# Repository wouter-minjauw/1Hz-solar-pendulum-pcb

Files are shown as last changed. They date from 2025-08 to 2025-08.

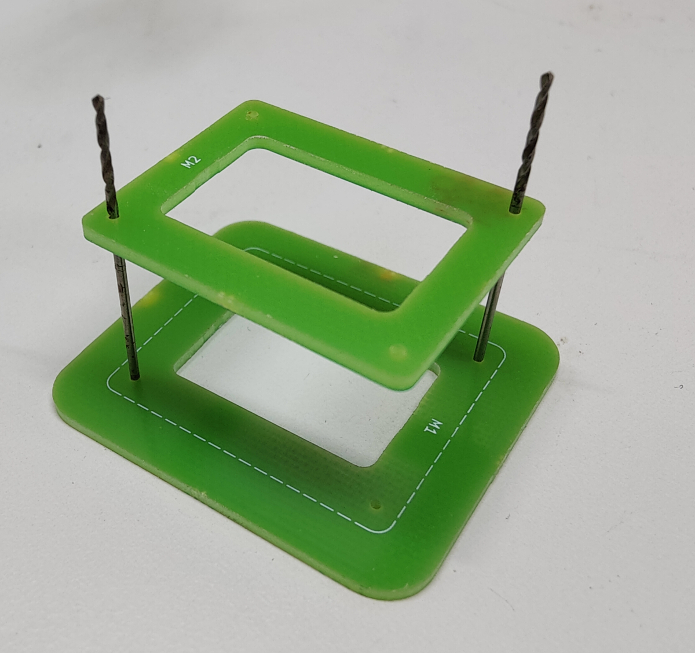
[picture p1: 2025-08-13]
pictures/coils/coil_former_assembly.jpg

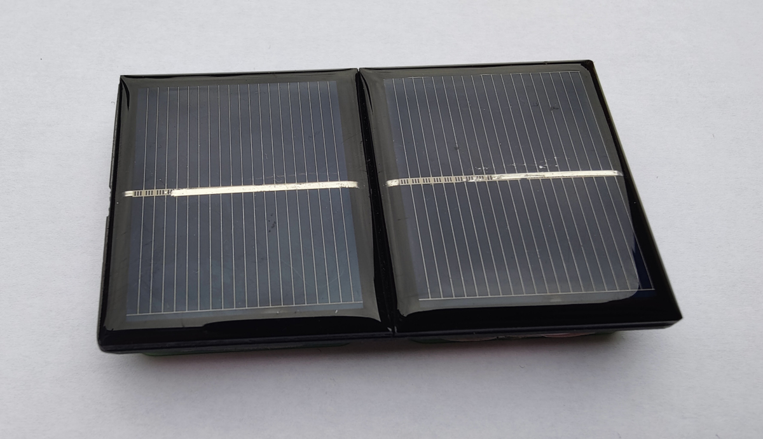
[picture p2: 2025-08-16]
pictures/coils/final_assembly_front.jpg

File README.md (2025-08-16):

# A 1Hz solar powered pendulum without transistors
## The pendulum
Nothing shows more what this is all about than a simple video of the pendulum in operation.

https://github.com/user-attachments/assets/9172c2cc-38bf-4e86-9793-8a3549da9c43

## The idea behind it
The idea behind this project was to create a solar powered pendulum in the simplest way possible, without any transistors. This is easier said than done, as most of us know how to design with transistors, but we have lost the knowledge to design something without them.

## The problem that needs to be solved
The problem is that in order to make the pendulum oscillate, some sort of AC force must be applied to the pendulum, but a solar cell provides DC output. So the main problem boils down to **can you generate an AC force on a mechanical system by using DC solar cells.**

The answer is yes, but it requires some out of the box thinking, and some may consider the solution as 'cheating'. However, the goal was not to use transistors, so anything is allowed as long as no transistors are used.

## Generating force
To generate force on the pendulum, a magnet is put on the pendulum, and coils are used below the magnet to push the magnet. The picture below shows a cross section of the two coils that are used in the device, and how current should be passed through them in order to generate a magnetic force to the right or to the left, depending on the direction of the current through the coils.
magnet_and_coils

## Creating an AC source with DC solar cells
If no transistors can be used to create an 'inverter' which turns DC into AC, a different solution is needed. A lot of experiments were performed with the pendulum partially shading it's own solar cell in order to get some AC voltage superimposed on the DC output of the solar cell, but the results were disappointing. Although you can get some AC voltage on top of the DC voltage, the power you can get out of it is very limited.

A much better solution turned out to be using two solar cells, and wiring them in anti-parallel, as can be seen in the following schematic of the device.

schematic

Each solar cell can be modeled as a light-dependent current source, with an intrinsic diode in parallel. If the pendulum is in the center, then both cells will be 50% shaded. The left solar cell pushes 200mA from GND to V_SOLAR, and the right solar cell pulls 200mA from V_SOLAR to GND. Both currents balance each other out, and no current flows through the intrinsic diodes of the cells, V_SOLAR is thereby 0V.

If the pendulum swings to the left, then the left solar cell will be (for instance) 75% shaded and the right solar cell 25% shaded. The left solar cell will now push 100mA from GND to V_SOLAR, the right solar cell will pull 300mA from V_SOLAR to GND. As Kirchoff's laws must be obeyed, 200mA will flow through the intrinsic diode of the right solar cell, resulting in V_SOLAR become a few hunderd millivolts negative. Similarly, if the pendulum swings to the right, V_SOLAR becomes a few hundred millivolts positive.

A sinusoidal movement of the pendulum results in a sinusoidal current of the solar cells, but due to the nonlinear I-V characteristic of the intrinsic diodes, the waveform of V_SOLAR starts to look more like a quare wave than a sine, which will turn out to be beneficial later on.

The pictures below show a simulation of the solar generator and the resulting V_SOLAR voltage. (The exact model of the diodes doesn't really matter, we just want to show the general behavior here.)

simulation_schematic
simulation_waveform

The dv/dt slope of the voltage is the highest at the zero crossings of the V_SOLAR, and this occurs when the pendulum passes through the mechanical center, shading both solar cells equally. Looking back at the magnetics picture earlier, this exactly when force should be generated on the magnet. In order to provide the right force at the right time, some capacitors in parallel are connected between V_SOLAR and the coils. Due to the I=C*dv/dt behavior of the capacitor, it will pass the most current through the coils at the zero crossings of the waveform, and that's exactly when we need it.

## The panelized PCB
A panelized PCB was made for this project, which contains a base PCB on which the solar cells are directly mounted, and some smaller PCBs which can be used to create coil formers. As I don't have a 3D printer yet, and needed a PCB anyway, it was the most economical solution to make the coil former out of PCB material.

All PCB's have 1mm alignment holes. The coil formers are built by using 1mm HSS drills as alignment guides, and stacking the different PCB's on top of each other with some superglue between them.

coil_former_assembly
assembled_coil_former

The coils are wound with 1000 turns of very fine wire. At the ends of the fine wire, a thicker wire was attached for mechanical rubustness, and the windings were covered with some paint masking tape for protection.

The final assembly looks like this:

final_assembly_front
final_assembly_back

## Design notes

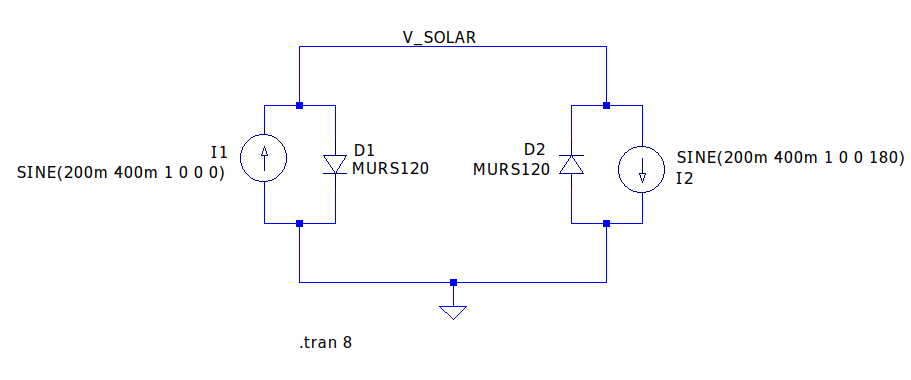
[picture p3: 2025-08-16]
pictures/theory_of_operation/simulation_schematic.png

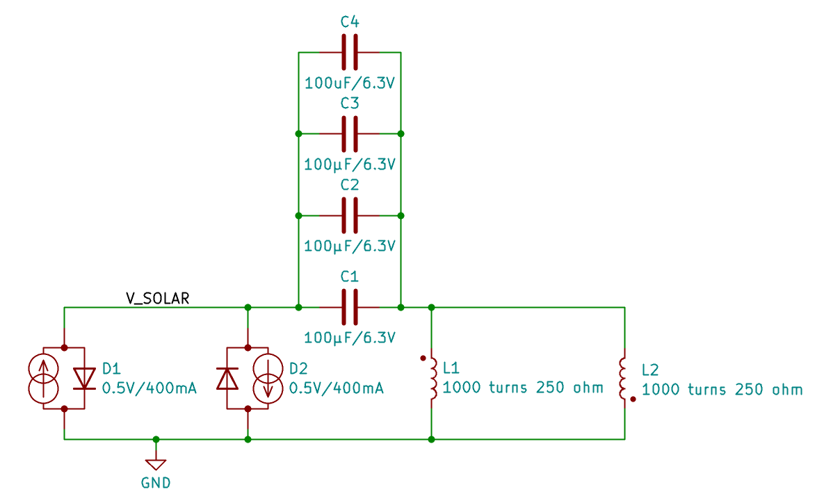
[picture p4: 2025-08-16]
pictures/theory_of_operation/schematic.png

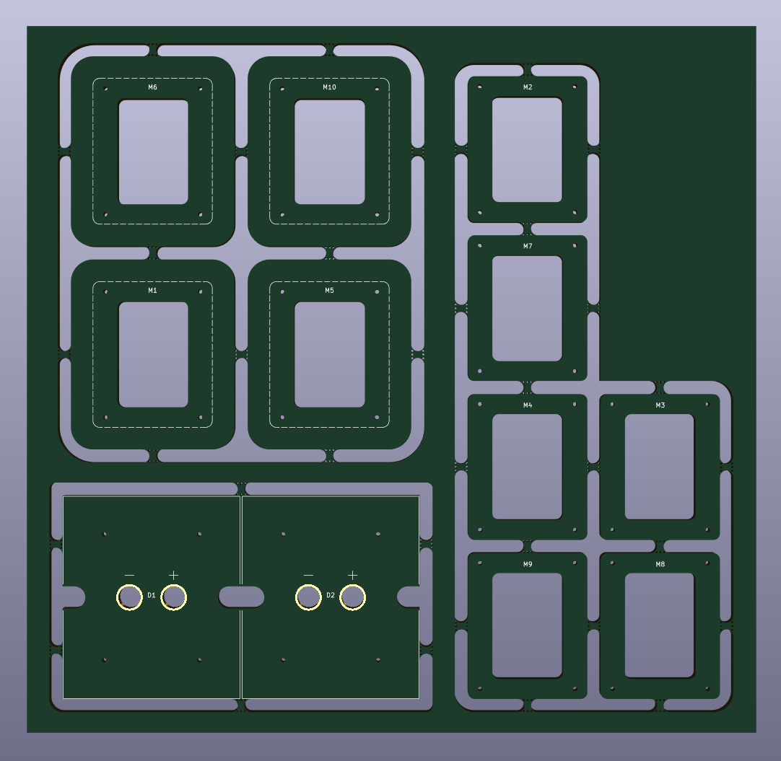
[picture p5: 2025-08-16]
pictures/panelized_pcb/panelized_pcb.png

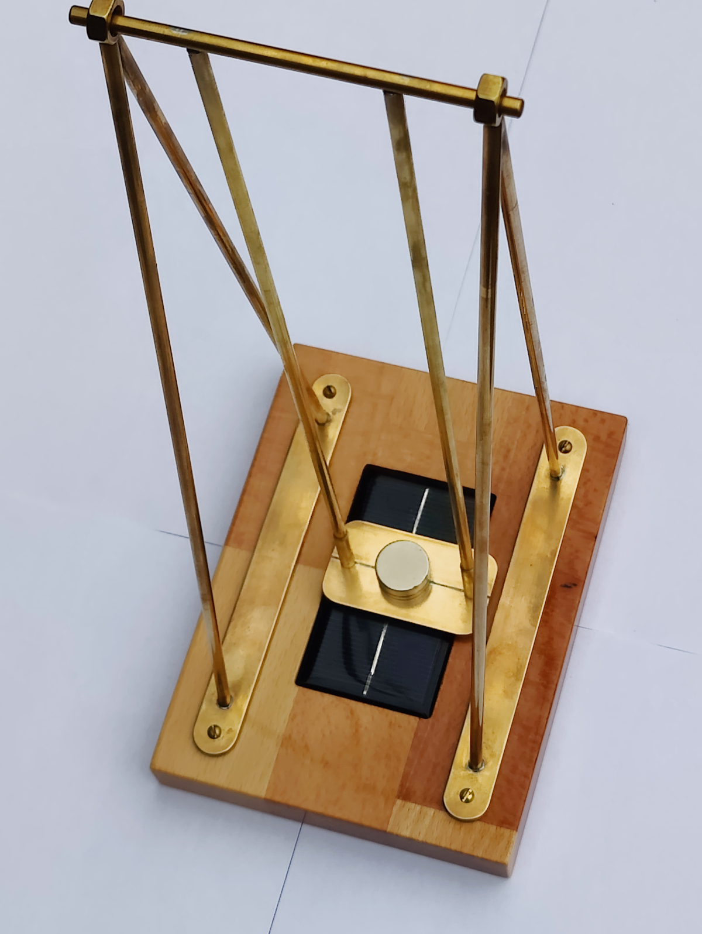
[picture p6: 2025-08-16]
pictures/pendulum/finished_pendulum.jpg

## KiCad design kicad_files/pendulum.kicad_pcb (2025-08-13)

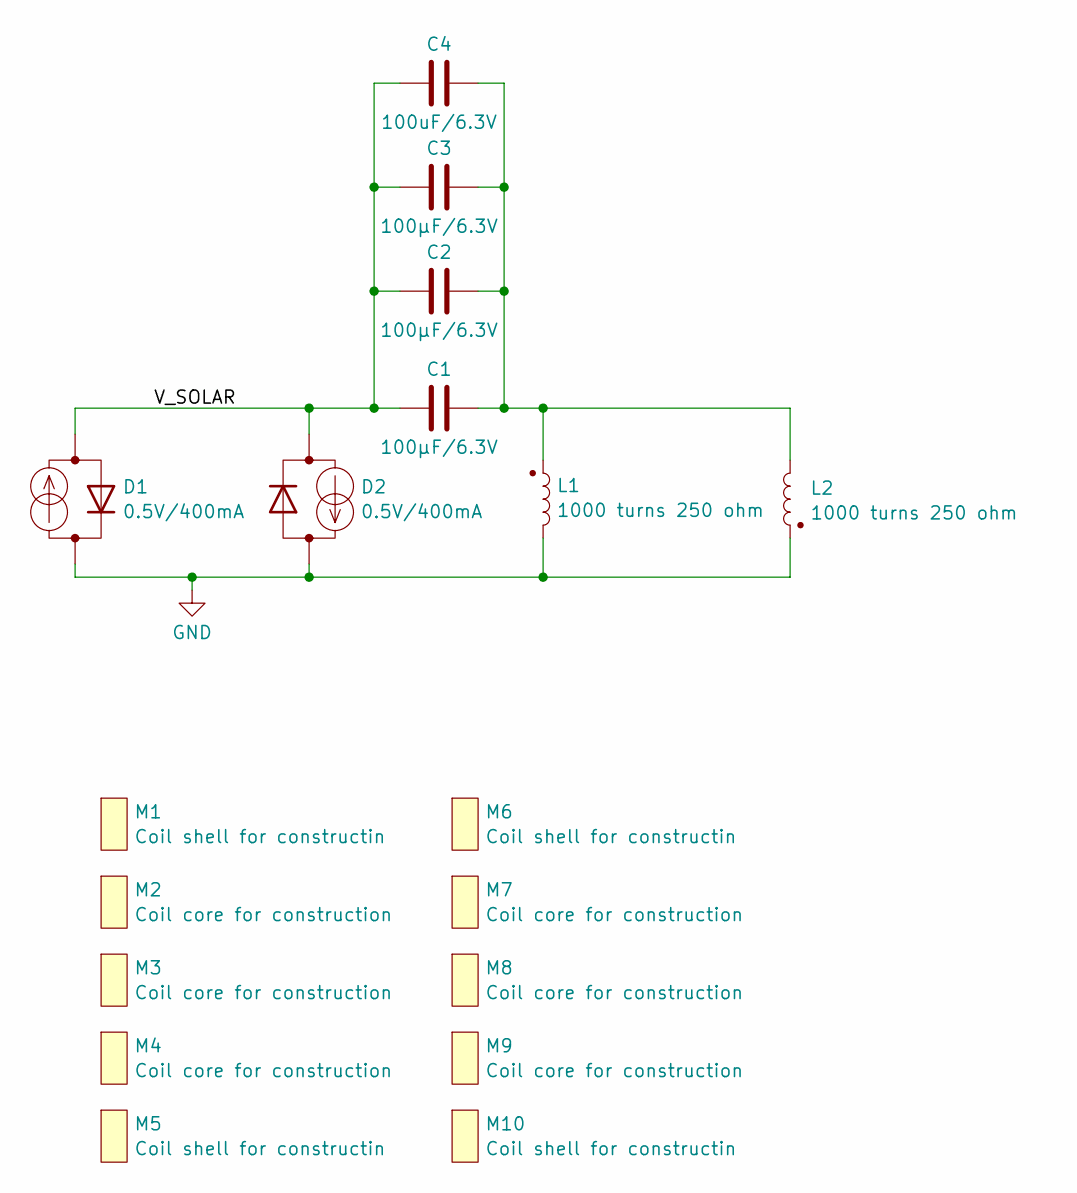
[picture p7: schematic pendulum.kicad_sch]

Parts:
C1, C2, C3: 100µF/6.3V; C_1206_3216Metric_Pad1.33x1.80mm_HandSolder
C4: 100uF/6.3V; C_1206_3216Metric_Pad1.33x1.80mm_HandSolder
D1, D2: 0.5V/400mA; solar_cell
L1, L2: 1000 turns 250 ohm; coil
M1, M5, M6, M10: Coil shell for constructin; coil_shell_for_construction
M2, M3, M4, M7, M8, M9: Coil core for construction; coil_core_for_construction

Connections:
unnamed: C1.2, C2.2, C3.2, C4.2, L1.1, L2.2
unnamed: C1.1, C2.1, C3.1, C4.1, D1.1 (A), D2.2 (K)
unnamed: D1.2 (K), D2.1 (A), L1.2, L2.1

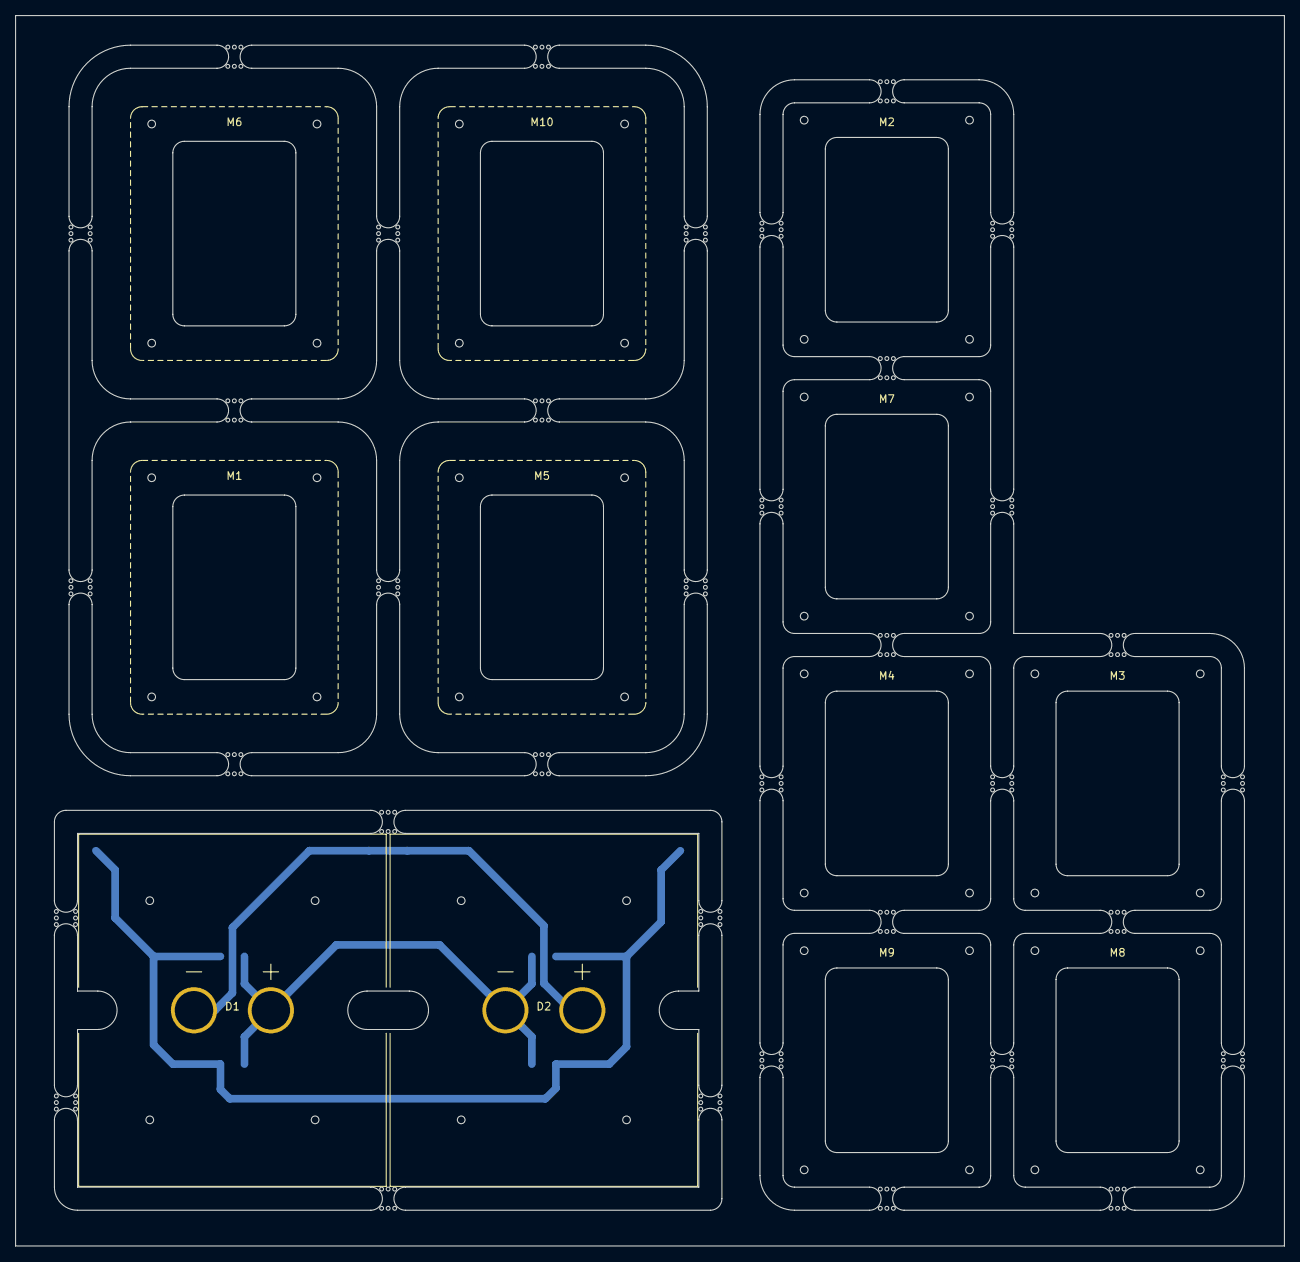
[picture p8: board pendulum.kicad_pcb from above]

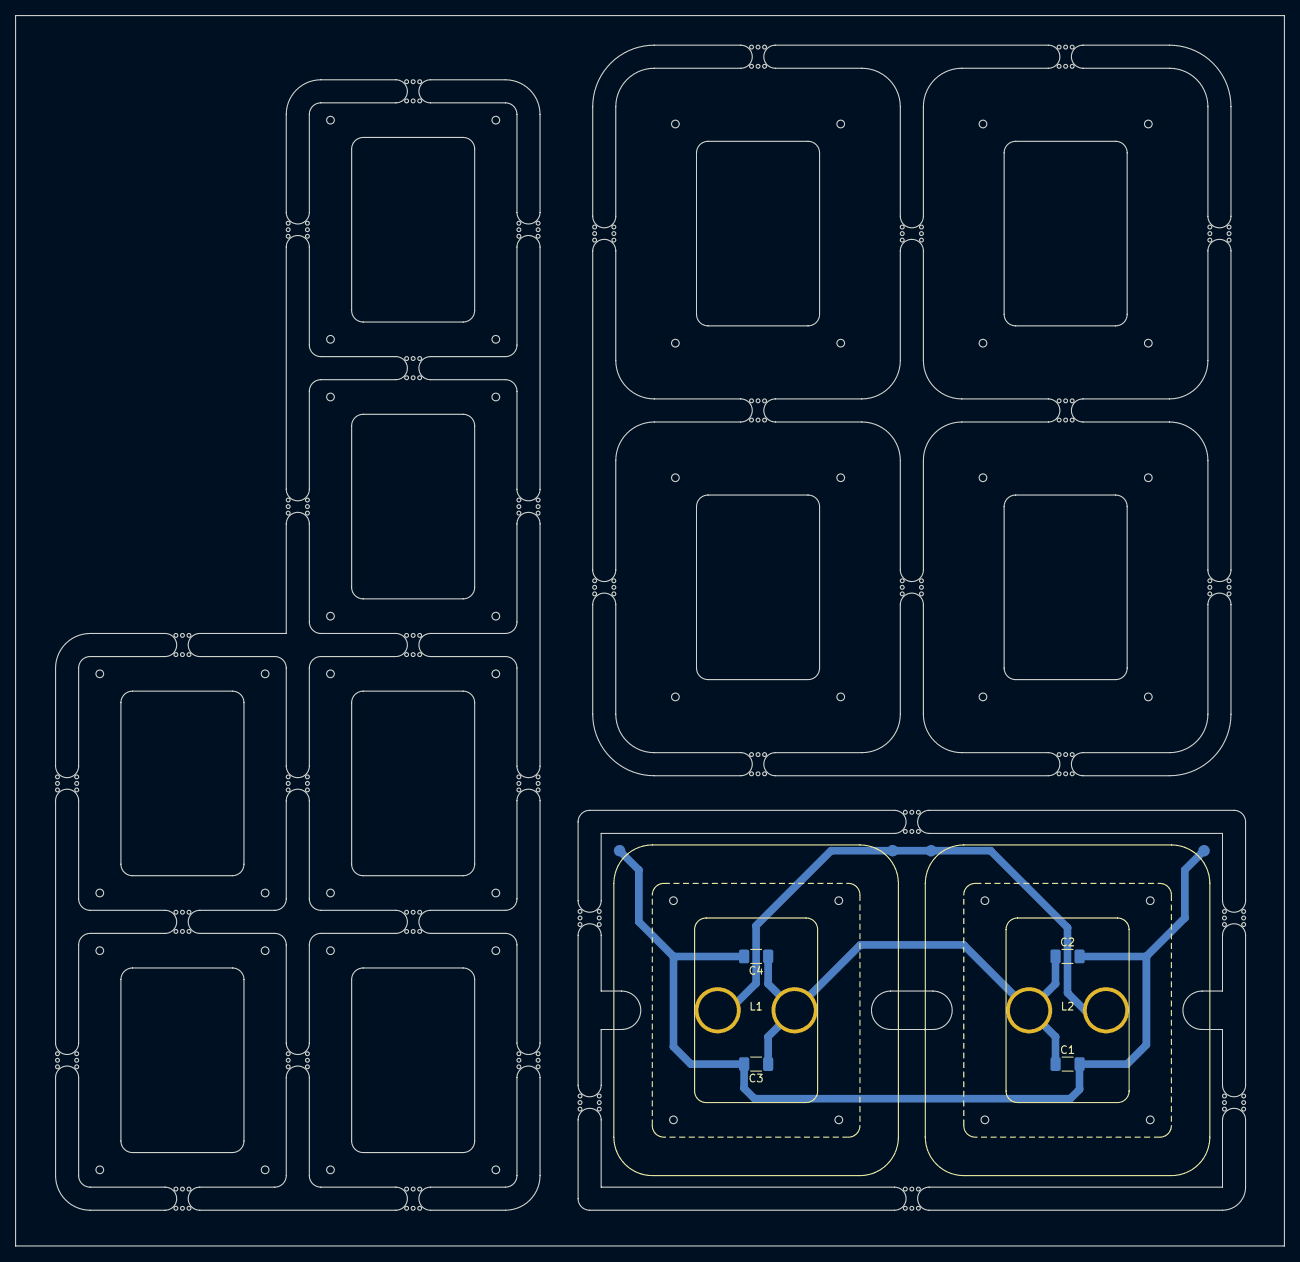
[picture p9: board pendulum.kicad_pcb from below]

Board: 2 copper layers, 165.0 x 160.0 mm, 18 parts (6 on the bottom side), 3 nets.

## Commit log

2025-08-13 Adds kicad project and pictures.
    [pendulum-B_Cu.gbr, pendulum-B_Mask.gbr, pendulum-B_Silkscreen.gbr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]
2025-08-16 Updates pictures, directory structures, and simulation
    [pendulum-B_Cu.gbr, pendulum-B_Mask.gbr, pendulum-B_Silkscreen.gbr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]
